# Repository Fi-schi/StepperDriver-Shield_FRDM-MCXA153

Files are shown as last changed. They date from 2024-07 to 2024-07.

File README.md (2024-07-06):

# StepperDriver-Shield_FRDM-MCXA153

This is a shield for the FRDM-MCXA153 microcontroller, developed as part of my mechatronic course project at the Hochschule Wismar, University of Applied Sciences: Technology, Economy and Design.

The board acts as a carrier for the TMC-2209 stepper drivers and allows up to four stepper motors to be controlled simultaneously.

It is designed for 24V operation and has three freely programmable buttons, connections for four limit switches and a manual stepper driver enable circuit.
In addition, by soldering a DC-DC converter to the microcontroller, it is possible to supply 24V through the shield.

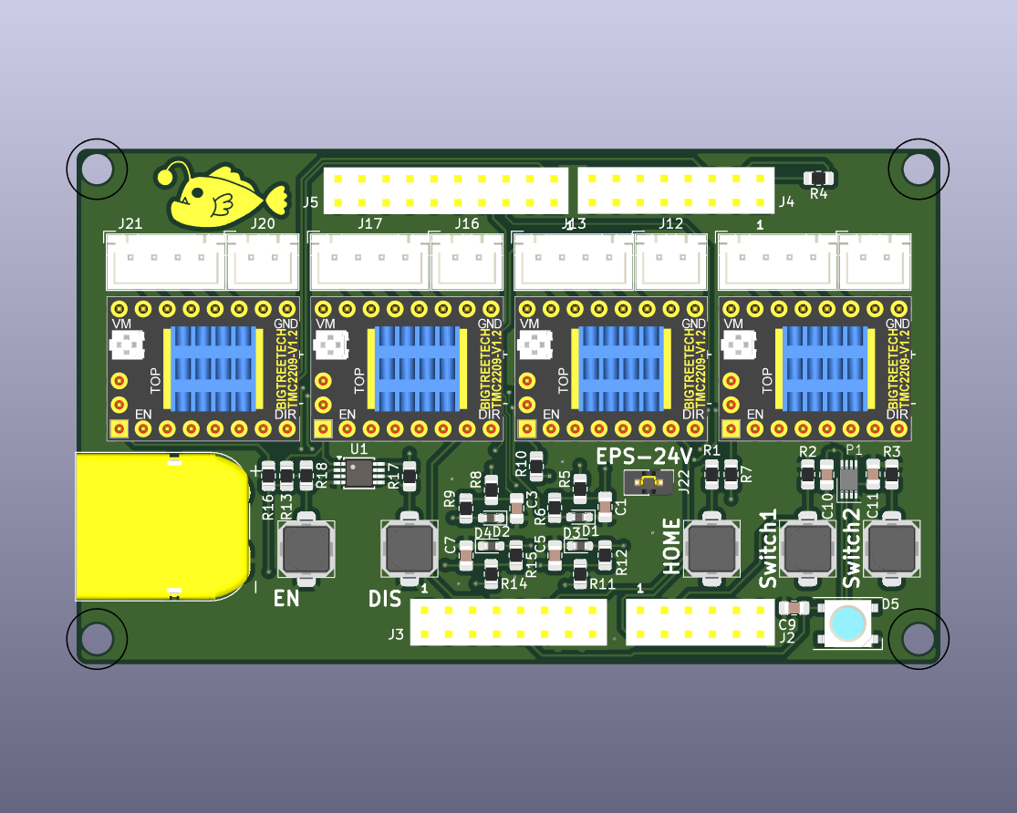
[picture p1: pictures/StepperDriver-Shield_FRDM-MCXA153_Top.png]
StepperDriver-Shield_FRDM-MCXA153_Top

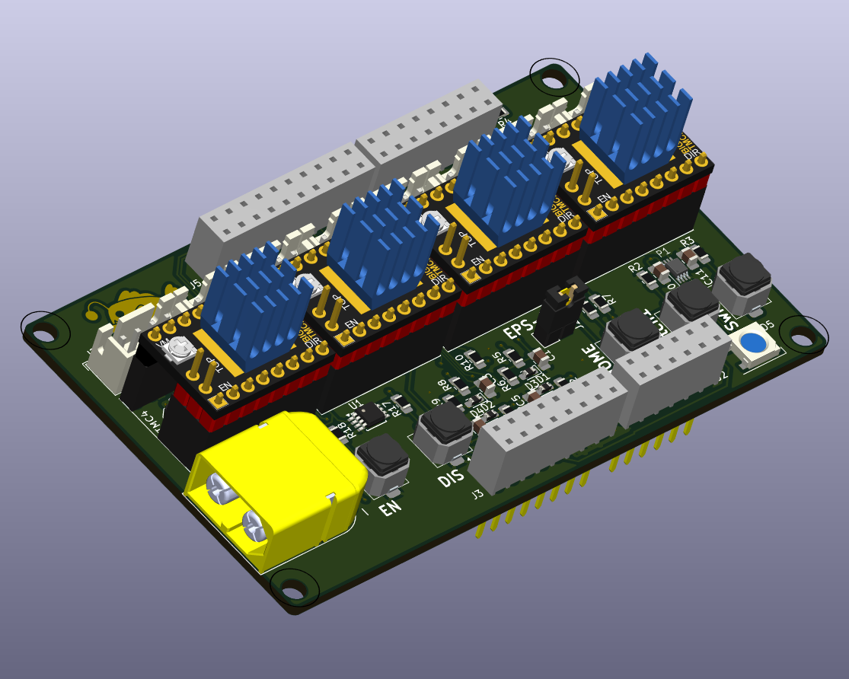
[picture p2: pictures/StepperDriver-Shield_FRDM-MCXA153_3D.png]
StepperDriver-Shield_FRDM-MCXA153_3D


# Parts for the shield

| Qty. | Part | Size | Links |
|---|:---:|:---:|:---|
|  7x  | 0.1µF | 0805 |  |
|  4x  | 100µF/35V  | 6.3mm  | https://www.mouser.de/ProductDetail/661-EMZR350ARA101MF6 |
|  13x | 10K&Omega; | 0805 |  |
|  4x  | 100&Omega; | 0805 |  |
|  1x  | 1K&Omega;  | 0805 |  |
|  4x  |TVS-Diode 3.3V | 0603 | https://www.mouser.de/ProductDetail/652-CG0603MLC-3.3LE |
|  1x  | 74LVC2G00 |TSSOP-8 | https://www.mouser.de/ProductDetail/771-LVC2G00DP125 |
|  1x  |SN74LXC2T45-Q1 | 	VSSOP | https://www.mouser.de/ProductDetail/595-74LXC2T45QDCURQ1 |
|  1x  | WS2812B | |  | 
|  5x  |Tactile Switch | 6x6mm  | https://www.mouser.de/ProductDetail/710-430133050816 |
|  4x  | 1x02 JST_XH | 2,54mm |  |
|  4x  | 1x04 JST_XH | 2,54mm |  |
|  1x  | 1x02 PinHeader| 2,54mm |  |
|  8x  | 1x03 PinHeader| 2,54mm |  |
|  9x  | Pin Header Jumper | 2,54mm |  |
|  1x  | AMASS XT60PW-M| |  |
|  1x  | 2x06 PinHeader (SSW-106-23-G-D) | 2,54mm| https://www.samtec.com/de/products/ssw-106-23-g-d |
|  1x  | 2x08 PinHeader (SSW-108-23-G-D) | 2,54mm| https://www.samtec.com/de/products/ssw-108-23-g-d |
|  2x  | 3x10 PinHeader (SSW-110-23-G-D) | 2,54mm| https://www.samtec.com/de/products/ssw-110-23-g-d |
|  4x  | BTT TMC2019 Stepp Stick | |  |

# Parts for the microcontroller external power supply

| Qty. | Part | Size | Links |
|---|:---:|:---:|:---|
|  1x  | DC/DC to 5v/500mA| SIP-3  | https://www.mouser.de/ProductDetail/919-R-78CK5.0-0.5 |
|  2x  | 1µF/35V  | 0603  |  |

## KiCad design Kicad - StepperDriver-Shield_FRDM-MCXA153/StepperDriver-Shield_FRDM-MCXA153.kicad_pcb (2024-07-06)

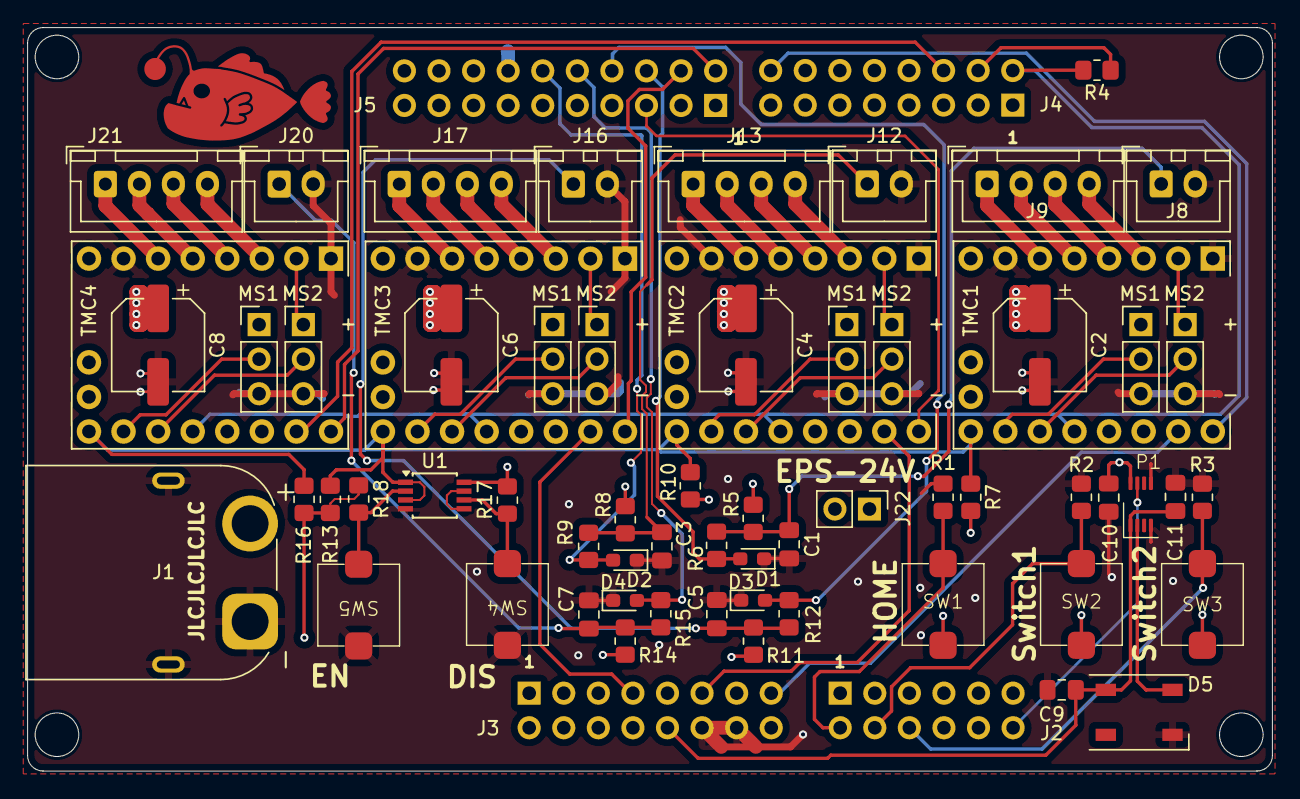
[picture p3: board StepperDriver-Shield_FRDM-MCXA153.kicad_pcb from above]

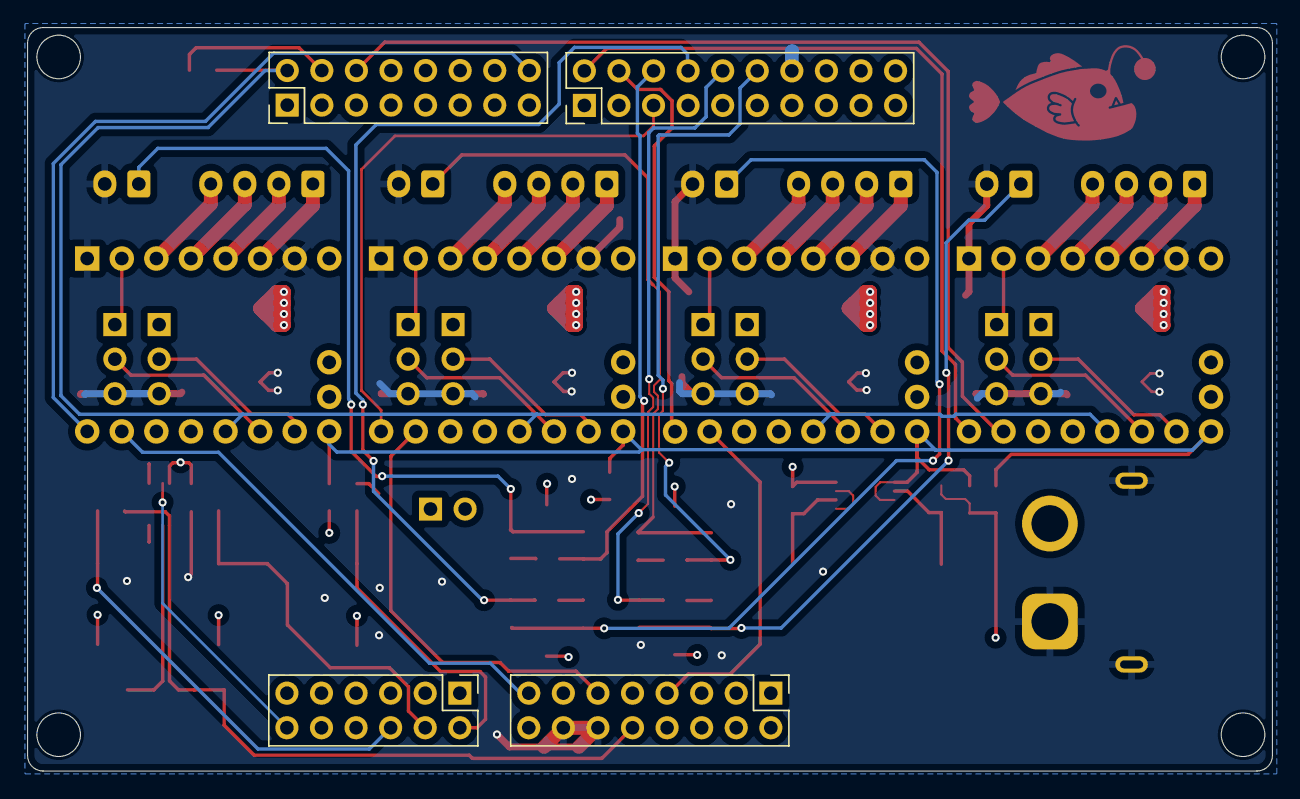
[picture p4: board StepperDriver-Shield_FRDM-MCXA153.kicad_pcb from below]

Board: 4 copper layers, 91.4 x 54.6 mm, 72 parts (4 on the bottom side), 56 nets.

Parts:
Blub1: Fischi
C1, C3, C5, C7: 0.1UF; C_0805_2012Metric_Pad1.18x1.45mm_HandSolder
C2, C4, C6, C8: 100UF/35V; CP_Elec_6.3x7.7
C9, C10, C11: 0.1µF; C_0805_2012Metric_Pad1.18x1.45mm_HandSolder
D1, D2, D3, D4: D_TVS; D_0603_1608Metric_Pad1.05x0.95mm_HandSolder
D5: WS2812B; LED_WS2812B_PLCC4_5.0x5.0mm_P3.2mm
H1, H2, H3, H4: Mechanical_MountingHole; MountingHole_3.2mm_M3
J1: Conn_01x02_Socket; AMASS_XT60PW-M
J2: SSQ-106-03-T-D; PinHeader_2x06_P2.54mm_Vertical
J3, J4: SSQ-108-03-T-D; PinHeader_2x08_P2.54mm_Vertical
J5: SSQ-110-03-T-D; PinHeader_2x10_P2.54mm_Vertical
J6, J7, J10, J11, J14, J15, J18, J19: Conn_01x03; PinHeader_1x03_P2.54mm_Vertical
J8, J12, J16, J20: Conn_01x02_Pin; JST_XH_B2B-XH-A_1x02_P2.50mm_Vertical
J9, J13, J17, J21: Conn_01x04_Pin; JST_XH_B4B-XH-A_1x04_P2.50mm_Vertical
J22: Conn_01x02_Socket; PinHeader_1x02_P2.54mm_Vertical
P1: SN74LXC2T45QDCURQ1_; SN74LXC2T45QDCURQ1
R1, R2, R3, R5, R7, R8, R10, R11, R13, R14, R16, R17, R18: 10K; R_0805_2012Metric_Pad1.20x1.40mm_HandSolder
R4: 1K; R_0805_2012Metric_Pad1.20x1.40mm_HandSolder
R6, R9, R12, R15: 100R; R_0805_2012Metric_Pad1.20x1.40mm_HandSolder
SW1: Home; Takt_Schalter_Aliexpress
SW2: SW1; Takt_Schalter_Aliexpress
SW3: SW2; Takt_Schalter_Aliexpress
SW4: DIS; Takt_Schalter_Aliexpress
SW5: EN; Takt_Schalter_Aliexpress
TMC1, TMC2, TMC3, TMC4: TMC2209; Btt_TMC2209_V1.3
U1: 74LVC2G00; TSSOP-8_3x3mm_P0.65mm

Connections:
5v-9v: J3.16, J22.1
/EN_Logic/ENABLE: U1.5, U1.7
/P1-4/UART2-RXD: J4.2, R4.2, TMC1.14 (RX), TMC2.14 (RX), TMC3.14 (RX), TMC4.14 (RX)
/P1-5/UART2-TXD: J4.4, R4.1
/P1-10/ADC0-A8: J2.2, R1.1, SW1.1
/P1-12/ADC0-A10: J2.4, R2.1, SW2.1
/P1-13/ADC0-A11: J2.6, R3.1, SW3.1
/P2-3/ADC0-A2: J5.5, TMC2.18 (DIR)
/P2-4/GPIO: J4.6, TMC4.17 (STEP)
/P2-6/CSI1: D1.2 (A2), J5.6, R6.2
/P2-12/SCK1: D2.2 (A2), J5.12, R9.2
/P2-13/SDO1: D3.2 (A2), J5.8, R12.2
/P2-16/SDI1: D4.2 (A2), J5.10, R15.2
/P3-1/GPIO: J4.16, TMC1.18 (DIR)
/P3-6/PWM0-A0: J3.15, TMC1.17 (STEP)
/P3-8/PWM0-A1: J3.11, TMC2.17 (STEP)
/P3-10/PWM0-A2: J3.7, TMC3.17 (STEP)
/P3-14/PWM0-X2: J5.4, TMC3.18 (DIR)
/P3-15/GPIO: J5.2, TMC4.18 (DIR)
/P3-30/ADC0-A13: J2.12, P1.7 (B1)
/TMC_2209_wiring1/A1: J13.2, TMC2.5 (A1)
/TMC_2209_wiring1/A2: J13.1, TMC2.6 (A2)
/TMC_2209_wiring1/B1: J13.3, TMC2.4 (B1)
/TMC_2209_wiring1/B2: J13.4, TMC2.3 (B2)
/TMC_2209_wiring1/MS1: J11.2, TMC2.12 (MS1)
/TMC_2209_wiring1/MS2: J10.2, TMC2.13 (MS2)
/TMC_2209_wiring2/A1: J17.2, TMC3.5 (A1)
/TMC_2209_wiring2/A2: J17.1, TMC3.6 (A2)
/TMC_2209_wiring2/B1: J17.3, TMC3.4 (B1)
/TMC_2209_wiring2/B2: J17.4, TMC3.3 (B2)
/TMC_2209_wiring2/MS1: J15.2, TMC3.12 (MS1)
/TMC_2209_wiring2/MS2: J14.2, TMC3.13 (MS2)
/TMC_2209_wiring3/A1: J21.2, TMC4.5 (A1)
/TMC_2209_wiring3/A2: J21.1, TMC4.6 (A2)
/TMC_2209_wiring3/B1: J21.3, TMC4.4 (B1)
/TMC_2209_wiring3/B2: J21.4, TMC4.3 (B2)
/TMC_2209_wiring3/MS1: J19.2, TMC4.12 (MS1)
/TMC_2209_wiring3/MS2: J18.2, TMC4.13 (MS2)
/TMC_2209_wiring/A1: J9.2, TMC1.5 (A1)
/TMC_2209_wiring/A2: J9.1, TMC1.6 (A2)
/TMC_2209_wiring/B1: J9.3, TMC1.4 (B1)
/TMC_2209_wiring/B2: J9.4, TMC1.3 (B2)
/TMC_2209_wiring/MS1: J7.2, TMC1.12 (MS1)
/TMC_2209_wiring/MS2: J6.2, TMC1.13 (MS2)
//ENABLE: R7.1, R10.1, R13.1, R16.1, TMC1.11 (/EN), TMC2.11 (/EN), TMC3.11 (/EN), TMC4.11 (/EN), U1.1, U1.3
GND: C1.2, C2.2, C3.2, C4.2, C5.2, C6.2, C7.2, C8.2, C9.1, C10.1, C11.2, D1.1 (A1), D2.1 (A1), D3.1 (A1), D4.1 (A1), D5.3 (VSS), J1.1, J3.12, J3.14, J5.14, J6.3, J7.3, J8.2, J10.3, J11.3, J12.2, J14.3, J15.3, J16.2, J18.3, J19.3, J20.2, P1.4 (GND), P1.5 (DIR), R1.2, R2.2, R3.2, SW4.1, SW5.1, TMC1.1 (GND), TMC1.7 (GND), TMC2.1 (GND), TMC2.7 (GND), TMC3.1 (GND), TMC3.7 (GND), TMC4.1 (GND), TMC4.7 (GND), U1.4 (GND)
unnamed: D5.4 (DIN), P1.2 (A1)
unnamed: C1.1, J8.1, R5.1, R6.1
unnamed: C3.1, J12.1, R8.1, R9.1
unnamed: C5.1, J16.1, R11.1, R12.1
unnamed: C7.1, J20.1, R14.1, R15.1
unnamed: R17.2, SW4.2, U1.6
unnamed: R18.2, SW5.2, U1.2
SYS-5V: C9.2, C11.1, D5.1 (VDD), J3.10, P1.1 (VCC_A)
Vcc_Logic: C10.2, J3.8, J6.1, J7.1, J10.1, J11.1, J14.1, J15.1, J18.1, J19.1, P1.8 (VCC_B), R5.2, R7.2, R8.2, R10.2, R11.2, R13.2, R14.2, R16.2, R17.1, R18.1, SW1.2, SW2.2, SW3.2, TMC1.2 (V_IO), TMC2.2 (V_IO), TMC3.2 (V_IO), TMC4.2 (V_IO), U1.8 (VCC)
Vcc_Motor: C2.1, C4.1, C6.1, C8.1, J1.2, J22.2, TMC1.8 (VS), TMC2.8 (VS), TMC3.8 (VS), TMC4.8 (VS)

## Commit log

2024-04-26 first push
    [EN_Logic.kicad_sch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]
2024-06-29 New Revision
    [EN_Logic.kicad_sch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]
2024-06-29 Update 3D Models
    [StepperDriver-Shield_FRDM-MCXA153.kicad_pcb, StepperDriver-Shield_FRDM-MCXA153.kicad_sch]
2024-06-30 Update gerber to order
    [StepperDriver-Shield_FRDM-MCXA153-B_Cu.gbr, StepperDriver-Shield_FRDM-MCXA153-B_Mask.gbr, StepperDriver-Shield_FRDM-MCXA153-B_Silks.gbr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]
2024-07-06 Added Status RGB LED
    [StepperDriver-Shield_FRDM-MCXA153.kicad_pcb, StepperDriver-Shield_FRDM-MCXA153.kicad_sch]
2024-07-06 Update Gerber Files
    [StepperDriver-Shield_FRDM-MCXA153-B_Cu.gbr, StepperDriver-Shield_FRDM-MCXA153-B_Mask.gbr, StepperDriver-Shield_FRDM-MCXA153-B_Silks.gbr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]
